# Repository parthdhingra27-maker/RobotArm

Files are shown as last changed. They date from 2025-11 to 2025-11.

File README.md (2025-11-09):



<h1 align="center">UtiliArm: A Custom Open Source 5-DOF Robotic Arm</h1>
<p align="center">Project Files:</p>

<p align="center">
  <a href="https://cad.onshape.com/documents/7d4782fc1d2b81b2411dc364/w/61aa74bc50ffa663fe78e913/e/d61dc358418eba5ccd3d28ce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">Onshape CAD Files</a> •
  <a href="https://docs.google.com/spreadsheets/d/1jZwi7d67DiPdZLEvy5LfeC6HyOPPZ9pO3xaRMX1j6oo/edit?usp=sharing">Bill of Materials</a> •
  <a href="https://blueprint.hackclub.com/projects/599">Blueprint Journal</a>
</p>

I made this to learn more about how robot arms work, how they are designed, controlled, and the types of end-effectors that can be used on them. Once I finish this arm, I want to be able to design different types of end-effectors that can go on the end of this. I also wanted to learn how to design a custom PCB as well as a custom wireless UI that can control this.

## Features
- 5 Degrees of Freedom: The base rotates and tilts, the arm tilts, and the wrist rotates and tilts, allowing for easy movement.
- Cost-Effective: This robot arm with a custom PCB and all parts included costs around $300 to build, making it cost-effective.
- Wireless Control: This arm is powered by an ESP 32 microcontroller with has WIFI capability
- Custom UI: This project also includes a custom UI that will connect to the ESP to control the arm wirelessly from a laptop.
- Encoder Compatibility: This arm uses AS5600 encoders on each stepper motor joint, which allows you to get absolute encoder values and create programs to make the arm go to certain positions.
- Mostly 3D Printed: This arm is mostly 3D printed and doesn't require any machined parts or gearboxes.
- Includes an Emergency Stop
- Will include a fully wireless handheld control panel in the future.

## Design and CAD

The Onshape link can be found at the top of the README.
Each part of the arm is printed separately and then put together using M3 and M4 hardware and heat-set inserts that melt into the plastic using a soldering iron. Bearings are press fit. The pulleys each use a specific belt size, which means there is no need to cut belts. The pulleys are spaced to perfectly fit the belts and tension them properly, which also means no belt tensioners are needed.

This is the base. The top part rotates on bearings and is screwed in from the bottom so it doesn't fall off.



This is the big pulley that tilts the arm. It sits in the bearings, which are shown in the part above.



This is the Arm and the part that holds the arm. It includes a mount on the right side for the AS5600 encoder.




This is the wrist and the part that mounts the wrist onto the arm. The wrist just connects to a stepper motor that allows it to rotate. The wrist uses an MG996R Servo to tilt up and down.




This is the full assembly:



## PCB and Schematics:

This is the schematic for the custom PCB. The arm is powered from a bench power supply. There is a buck converter that converts into 5V. The main microcontroller is an ESP32 and there are three stepper drivers, slots for servo motors, an external Nema 23 driver, an I2C multiplexer for encoders,s and an expansion slot to add another PCB later on. There is also a screw terminal for an E-Stop. The PCB also has a GND pour and VIA's connecting the layers.





## Bill of Materials
These are the components needed. The prices and links can be found here:  <a href="https://docs.google.com/spreadsheets/d/1jZwi7d67DiPdZLEvy5LfeC6HyOPPZ9pO3xaRMX1j6oo/edit?usp=sharing">Bill of Materials Google Sheets</a>

- 1 PCB
- All 3D printed parts
- 3 x Nema 17 Motors
- 1 x Nema 23 Motor
- 3 x TMC2209 Drivers
- 1 x ESP32 Dev Kit
- 1 x TB6600 Driver
- Solder
- Solder Flux
- 3 x AS5600 Magnet Encoders
- 8 x 4x10x4 Bearings
- 8 x 20mm x 47mm x 14mm Bearings
- 1 x GT2 600mm Timing Belt
- 2 x GT2 400mm Timing Belt
- 1 x GT2 420mm Timing Belt
- 5 x 20t Pulleys
- 3 x 5mm to 5mm Shaft Couplers
- 1 x 5mm Shaft
- 8 x 5mm Shaft Collars
- 1 x E-Stop Button
- 1 x TC9548A I2C Multiplexer
- 1 x LM2596 24v to 5v Buck Convertor
- 1 x KF301-2P Screw Terminal
- 1 x XT60 to Banana Plug Cable
- 1 x XT60 to PCB Connector
- 1 x LED
- 1 x 1x3 Headers Pack
- 1 x 1x6 Headers Pack
- 1 x JST-XH-4Pin Connectors Pack
- 1 x 6 Pin Screw Terminals Pack
- 1 x 220R Resistor
- 3 x 0.1uF Capacitors
- 3 x 100 uF Capacitors
- 1 x SS54 Input Diode
- 1 x Pack of M3 M4 Hardware
- 1 x Pack of M4 Heat Set Inserts
- 1 x Pack of Jumper Cables
- 1 x Pack of Heat Shrink for Cables
- 1 x 12x12 Piece of Wood for Base
- 1.5kg x PLA Filament
- 1 x Pack of M2x6mm Philips Head Screws

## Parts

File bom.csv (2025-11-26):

Part Name | Link | Vendor | Qty | Price Per Unit | Total Item Price | Notes | Current Part List (ignore)
Nema 17 Motor | https://www.aliexpress.us/item/3256808273084374.html?mp=1 | Aliexpress | 3 | $5.64 | $16.92 |  | Nema 17 Stepper Motors | TRUE
Nema 23 Motor | https://www.aliexpress.us/item/3256802160042515.html?curPageLogUid=FHrUbtzIm8Mn | Aliexpress | 1 | $23.27 | $23.27 | Cheaper on Amazon | Nema 23 Stepper Motors | TRUE
TMC2209 Drivers | https://www.aliexpress.us/item/2251832841735393.html?curPageLogUid=BcBVglVJW3Tj | Aliexpress | 1 | $13.74 | $13.74 | For Nema 17 Steppers | Stepper Drivers | TRUE
ESP 32 Dev Kit | https://www.amazon.com/ESP-WROOM-32-Development-Microcontroller-Integrated-Compatible/dp/B07WCG1PLV | Amazon | 1 | $8.99 | $8.99 | Cheaper with Shipping on Amazon | Filament - 2kg? | TRUE | Need Gram Amount
TB6600 Driver | https://www.aliexpress.us/item/3256805834107894.html?curPageLogUid=yXXbew8gJGMa | Aliexpress | 1 | $6.24 | $6.24 |  | Small Base Bearings | TRUE
PCB | https://drive.google.com/file/d/11k8NPm6qlL1cPLSDdq3B7cOSP-t6soDT/view?usp=sharing | JLCPCB | 1 | $5.30 | $5.30 | Includes Shipping | GT2 Timing Belt - multiple sizes | TRUE
Solder Flux | https://www.aliexpress.us/item/3256808722589055.html?curPageLogUid=kvXajsBk1s1i | Aliexpress | 1 | $1.95 | $1.95 |  | Big Bearings | TRUE
AS5600 Magnet Sensors | https://www.aliexpress.us/item/3256806163317817.html?curPageLogUid=SWjtwC5qpapB | Aliexpress | 1 | $5.42 | $5.42 | Encoders | Nema Compatible Pulleys | TRUE
Small Base Bearings - 4x10x4 | https://www.aliexpress.us/item/3256808665674212.html?curPageLogUid=9Ovk67vMtHG0 | Aliexpress | 2 | $3.12 | $6.24 |  | Wire - AWG + Jumper Wire | FALSE
6203 Pulley Bearings | https://www.aliexpress.us/item/3256808355977112.html?curPageLogUid=jWwpAysy2Age | Aliexpress | 3 | $4.26 | $12.78 | Cheaper on Amazon than Aliexpress for some reason | Stepper Motor Shaft Coupler | TRUE
Base Timing Belt - GT2 600mm | https://www.aliexpress.us/item/3256804460791382.html?curPageLogUid=6uxZZiebd3DN | Aliexpress | 1 | $3.52 | $3.52 |  | Steppr Motor Shaft Extension | TRUE
Tilt Timing Belt - GT2 400mm | https://www.aliexpress.us/item/3256808692490611.html?curPageLogUid=7w5KFZZBQcLW | Aliexpress | 2 | $4.93 | $9.86 |  | Hall Effect Magnet Sensors | TRUE
Arm Timing Belt - GT2 - 420mm | https://www.aliexpress.us/item/3256804906037786.html?curPageLogUid=88Y1iryqjXZD | Aliexpress | 1 | $3.66 | $3.66 |  | Solder Flux | TRUE
Nema Compatible Pulleys 20t | https://www.amazon.com/WINSINN-Aluminum-Synchronous-Timing-Printer/dp/B077GNZK3J | Amazon | 1 | $6.99 | $6.99 |  | PCB | TRUE
Nema Shaft Coupler - 5mm to 5mm | https://www.aliexpress.us/item/2251832618318567.html?curPageLogUid=BD9rcb5sGai2 | Aliexpress | 3 | $1.30 | $3.90 |  | Incorporate Screen? - already have | TRUE
5mm Shaft | https://www.aliexpress.us/item/3256804855023250.html?curPageLogUid=eToSzEbrcTHk | Aliexpress | 1 | $2.95 | $2.95 |  | Hardware | FALSE
5mm Bore Shaft Collars | https://www.amazon.com/uxcell-Collars-5-05mm-Collar-Carbon/dp/B0D2L23B34 | Amazon | 1 | $7.99 | $7.99 |  | Shaft Coupler | TRUE
Emergency Stop Button | https://www.aliexpress.us/item/3256805247269854.html?curPageLogUid=7iOAle9r2beF | Aliexpress | 1 | $3.16 | $3.16 |  | Shaft Collars | TRUE
TC9548A I2C Multiplexer | https://www.aliexpress.us/item/3256806776881856.html?curPageLogUid=IwMJi6b2YFbL | Aliexpress | 1 | $1.21 | $1.21 |  | Super Glue | TRUE
LM2596 Buck Convertor | https://www.aliexpress.us/item/3256807314089934.html?curPageLogUid=Wu6JDzB64eYc | Aliexpress | 1 | $1.83 | $1.83 |  | Threadlock | TRUE
KF301-2P | https://www.aliexpress.us/item/3256801470316663.html?curPageLogUid=JTMvVZ0UrrPF | Aliexpress | 1 | $2.03 | $2.03 | For 24v Power, TB6600, and EStop | Piece of plywood for base | FALSE
XT60 to Power Supply Cable | https://www.amazon.com/FLY-RC-Connector-Battery-Adapter/dp/B07C1QKNHP | Amazon | 1 | $7.99 | $7.99 |  | Heat Shrink for Wire | FALSE
XT60 to PCB Connector | https://www.aliexpress.us/item/3256807190011486.html?curPageLogUid=VTdH76DwQu0A | Aliexpress | 1 | $1.97 | $1.97 |  | Big Red E-Stop Button | TRUE
LED | https://www.aliexpress.us/item/3256803137393104.html?curPageLogUid=b62xWcd5ozFc | Aliexpress | 1 | $3.93 | $3.93 | For PCB |  | FALSE
1x3 Headers | https://www.aliexpress.us/item/2255800801798474.html?curPageLogUid=KULvQdnglpAk | Aliexpress | 1 | $1.62 | $1.62 | 1x3 Headers for Servo |  | FALSE
1x6 Headers | https://www.aliexpress.us/item/2255800801798474.html?curPageLogUid=KULvQdnglpAk | Aliexpress | 1 | $1.62 | $1.62 | 1x6 Header for the Expansion Slot on PCB | Electronics | FALSE
JST-XH-4Pin Connectors | https://www.aliexpress.us/item/3256806894018733.html?curPageLogUid=TLIAWzMVtzoH | Aliexpress | 1 | $2.41 | $2.41 | Stepper Connectors for the PCB |  | FALSE
6 Pin Screw Terminal | https://www.aliexpress.us/item/3256802765387985.html?curPageLogUid=IgnuE5tFisnK | Aliexpress | 1 | $2.98 | $2.98 | For TB6600 Data Connector | Esp 32 | TRUE
220R Resistor for LED | https://www.aliexpress.us/item/2251832766343175.html?curPageLogUid=BYePsJeal4NR | Aliexpress | 1 | $1.32 | $1.32 |  | Buck convertor | TRUE
0.1uF Capacitor for Drivers | https://www.digikey.com/en/products/detail/kemet/C0805C104K5RACTU/411169 | DigiKey | 3 | $0.08 | $0.24 | 4.99 shipping for DigiKey. Included in total | JST-XH 4-pin extension cables | FALSE
100uF Capacitor for Drivers | https://www.digikey.com/en/products/detail/rubycon/35ZLH100MEFC6-3X11/3134256 | DigiKey | 3 | $0.32 | $0.96 |  |  | FALSE
SS54 Input Diode | https://www.digikey.com/en/products/detail/shenzhen-slkormicro-semicon-co-ltd/SS54/21853075 | DigiKey | 1 | $0.18 | $0.18 |  |  | FALSE
M3 M4 Hardware | https://www.aliexpress.us/item/2255799852960451.html?mp=1 | Aliexpress | 1 | $14.00 | $14.00 | All the fasteners needed for the arm |  | FALSE
Heat Sunk Inserts | https://www.amazon.com/Inserts-3D-Printing-Accessories-Compatible-Soldering-Threaded/dp/B0CDRZN4B2 | Amazon | 1 | $8.99 | $8.99 | For all the hardware to plastic connections |  | FALSE
Jumper Cables | https://www.amazon.com/California-JOS-Breadboard-Optional-Multicolored/dp/B0BRTJXND9 | Amazon | 1 | $5.97 | $5.97 |  |  | FALSE
18 AWG Wire | https://www.aliexpress.us/item/3256806379805687.html?mp=1 | Aliexpress | 1 | $2.41 | $2.41 | Needed to connect the E-Stop |  | FALSE
Heat Shrink Wrap | https://www.aliexpress.us/item/3256807959988149.html?mp=1 | Aliexpress | 1 | $2.79 | $2.79 |  |  | FALSE
12x12 Piece of Wood | https://www.lowes.com/pd/Unbranded-1-4-in-x-2-ft-x-2-ft-Pine-Sanded-Plywood/5001992857 | Lowes | 1 | $7.78 | $7.78 | Piece of wood for the base of the robot to screw into and to mount electronics to. Cheapest one I could find |  | FALSE
M2x6mm Philips Screws | https://www.aliexpress.us/item/3256802119350443.html?curPageLogUid=bYjfPRmE1l1c | Aliexpress | 1 | $1.40 | $1.40 | For mounting the AS5600 Encoders |  | FALSE
 |  |  |  |  |  |  |  | FALSE
 |  |  |  |  |  |  |  | FALSE
 |  |  |  |  |  |  |  | FALSE
 |  |  |  |  |  |  |  | FALSE
Parts Total | $216.51 |  |  |  |  |  |  | FALSE
Shipping Total | $4.99 |  |  |  |  |  |  | FALSE
Subtotal | $221.50 |  |  |  |  |  |  | FALSE
Tax (Virginia 4.5%) | $9.97 |  |  |  |  |  |  | FALSE
Project Total | $231.47 |  |  |  |  |  |  | FALSE
 |  |  |  |  |  |  |  | FALSE
 |  |  |  |  |  |  |  | FALSE
 |  |  |  |  |  |  |  | FALSE
 |  |  |  |  |  |  |  | FALSE
 |  |  |  |  |  |  |  | FALSE
 |  |  |  |  |  |  |  | FALSE
 |  |  |  |  |  |  |  | FALSE
 |  |  |  |  |  |  |  | FALSE
 |  |  |  |  |  |  |  | FALSE
 |  |  |  |  |  |  |  | FALSE
 |  |  |  |  |  |  |  | FALSE
 |  |  |  |  |  |  |  | FALSE
 |  |  |  |  |  |  |  | FALSE
 |  |  |  |  |  |  |  | FALSE
 |  |  |  |  |  |  |  | FALSE
 |  |  |  |  |  |  |  | FALSE
 |  |  |  |  |  |  |  | FALSE
 |  |  |  |  |  |  |  | FALSE
 |  |  |  |  |  |  |  | FALSE
 |  |  |  |  |  |  |  | FALSE
 |  |  |  |  |  |  |  | FALSE
 |  |  |  |  |  |  |  | FALSE
 |  |  |  |  |  |  |  | FALSE
 |  |  |  |  |  |  |  | FALSE
 |  |  |  |  |  |  |  | FALSE
 |  |  |  |  |  |  |  | FALSE
 |  |  |  |  |  |  |  | FALSE
 |  |  |  |  |  |  |  | FALSE
 |  |  |  |  |  |  |  | FALSE
 |  |  |  |  |  |  |  | FALSE
 |  |  |  |  |  |  |  | FALSE
 |  |  |  |  |  |  |  | FALSE
 |  |  |  |  |  |  |  | FALSE
 |  |  |  |  |  |  |  | FALSE
 |  |  |  |  |  |  |  | FALSE
 |  |  |  |  |  |  |  | FALSE
 |  |  |  |  |  |  |  | FALSE
 |  |  |  |  |  |  |  | FALSE
 |  |  |  |  |  |  |  | FALSE
 |  |  |  |  |  |  |  | FALSE
 |  |  |  |  |  |  |  | FALSE
 |  |  |  |  |  |  |  | FALSE
 |  |  |  |  |  |  |  | FALSE
 |  |  |  |  |  |  |  | FALSE
 |  |  |  |  |  |  |  | FALSE
 |  |  |  |  |  |  |  | FALSE
 |  |  |  |  |  |  |  | FALSE
 |  |  |  |  |  |  |  | FALSE
 |  |  |  |  |  |  |  | FALSE
 |  |  |  |  |  |  |  | FALSE
 |  |  |  |  |  |  |  | FALSE
 |  |  |  |  |  |  |  | FALSE
 |  |  |  |  |  |  |  | FALSE
 |  |  |  |  |  |  |  | FALSE
 |  |  |  |  |  |  |  | FALSE
 |  |  |  |  |  |  |  | FALSE
 |  |  |  |  |  |  |  | FALSE
 |  |  |  |  |  |  |  | FALSE
 |  |  |  |  |  |  |  | FALSE
 |  |  |  |  |  |  |  | FALSE
 |  |  |  |  |  |  |  | FALSE
 |  |  |  |  |  |  |  | FALSE
 |  |  |  |  |  |  |  | FALSE
 |  |  |  |  |  |  |  | FALSE
 |  |  |  |  |  |  |  | FALSE
 |  |  |  |  |  |  |  | FALSE
 |  |  |  |  |  |  |  | FALSE
 |  |  |  |  |  |  |  | FALSE
 |  |  |  |  |  |  |  | FALSE
 |  |  |  |  |  |  |  | FALSE
 |  |  |  |  |  |  |  | FALSE
 |  |  |  |  |  |  |  | FALSE
 |  |  |  |  |  |  |  | FALSE
 |  |  |  |  |  |  |  | FALSE
 |  |  |  |  |  |  |  | FALSE
 |  |  |  |  |  |  |  | FALSE
 |  |  |  |  |  |  |  | FALSE
 |  |  |  |  |  |  |  | FALSE
 |  |  |  |  |  |  |  | FALSE
 |  |  |  |  |  |  |  | FALSE
 |  |  |  |  |  |  |  | FALSE
 |  |  |  |  |  |  |  | FALSE
 |  |  |  |  |  |  |  | FALSE
 |  |  |  |  |  |  |  | FALSE
 |  |  |  |  |  |  |  | FALSE
 |  |  |  |  |  |  |  | FALSE
 |  |  |  |  |  |  |  | FALSE
 |  |  |  |  |  |  |  | FALSE
 |  |  |  |  |  |  |  | FALSE
 |  |  |  |  |  |  |  | FALSE
 |  |  |  |  |  |  |  | FALSE
 |  |  |  |  |  |  |  | FALSE
 |  |  |  |  |  |  |  | FALSE
 |  |  |  |  |  |  |  | FALSE
 |  |  |  |  |  |  |  | FALSE
 |  |  |  |  |  |  |  | FALSE
 |  |  |  |  |  |  |  | FALSE
 |  |  |  |  |  |  |  | FALSE
 |  |  |  |  |  |  |  | FALSE
 |  |  |  |  |  |  |  | FALSE
 |  |  |  |  |  |  |  | FALSE
 |  |  |  |  |  |  |  | FALSE
 |  |  |  |  |  |  |  | FALSE
 |  |  |  |  |  |  |  | FALSE
 |  |  |  |  |  |  |  | FALSE
 |  |  |  |  |  |  |  | FALSE
 |  |  |  |  |  |  |  | FALSE
 |  |  |  |  |  |  |  | FALSE
 |  |  |  |  |  |  |  | FALSE
 |  |  |  |  |  |  |  | FALSE
 |  |  |  |  |  |  |  | FALSE
 |  |  |  |  |  |  |  | FALSE
 |  |  |  |  |  |  |  | FALSE
 |  |  |  |  |  |  |  | FALSE
 |  |  |  |  |  |  |  | FALSE
 |  |  |  |  |  |  |  | FALSE
 |  |  |  |  |  |  |  | FALSE
 |  |  |  |  |  |  |  | FALSE
 |  |  |  |  |  |  |  | FALSE
 |  |  |  |  |  |  |  | FALSE
 |  |  |  |  |  |  |  | FALSE
 |  |  |  |  |  |  |  | FALSE
 |  |  |  |  |  |  |  | FALSE
 |  |  |  |  |  |  |  | FALSE
 |  |  |  |  |  |  |  | FALSE
 |  |  |  |  |  |  |  | FALSE
 |  |  |  |  |  |  |  | FALSE
 |  |  |  |  |  |  |  | FALSE
 |  |  |  |  |  |  |  | FALSE
 |  |  |  |  |  |  |  | FALSE
 |  |  |  |  |  |  |  | FALSE
 |  |  |  |  |  |  |  | FALSE
 |  |  |  |  |  |  |  | FALSE
 |  |  |  |  |  |  |  | FALSE
 |  |  |  |  |  |  |  | FALSE
 |  |  |  |  |  |  |  | FALSE
 |  |  |  |  |  |  |  | FALSE
 |  |  |  |  |  |  |  | FALSE
 |  |  |  |  |  |  |  | FALSE
 |  |  |  |  |  |  |  | FALSE
 |  |  |  |  |  |  |  | FALSE
 |  |  |  |  |  |  |  | FALSE
 |  |  |  |  |  |  |  | FALSE
 |  |  |  |  |  |  |  | FALSE
 |  |  |  |  |  |  |  | FALSE
 |  |  |  |  |  |  |  | FALSE
 |  |  |  |  |  |  |  | FALSE
 |  |  |  |  |  |  |  | FALSE
 |  |  |  |  |  |  |  | FALSE
 |  |  |  |  |  |  |  | FALSE
 |  |  |  |  |  |  |  | FALSE
 |  |  |  |  |  |  |  | FALSE
 |  |  |  |  |  |  |  | FALSE
 |  |  |  |  |  |  |  | FALSE
 |  |  |  |  |  |  |  | FALSE
 |  |  |  |  |  |  |  | FALSE
 |  |  |  |  |  |  |  | FALSE
 |  |  |  |  |  |  |  | FALSE
 |  |  |  |  |  |  |  | FALSE
 |  |  |  |  |  |  |  | FALSE
 |  |  |  |  |  |  |  | FALSE
 |  |  |  |  |  |  |  | FALSE
 |  |  |  |  |  |  |  | FALSE
 |  |  |  |  |  |  |  | FALSE
 |  |  |  |  |  |  |  | FALSE
 |  |  |  |  |  |  |  | FALSE
 |  |  |  |  |  |  |  | FALSE
 |  |  |  |  |  |  |  | FALSE
 |  |  |  |  |  |  |  | FALSE
 |  |  |  |  |  |  |  | FALSE
 |  |  |  |  |  |  |  | FALSE
 |  |  |  |  |  |  |  | FALSE
 |  |  |  |  |  |  |  | FALSE
 |  |  |  |  |  |  |  | FALSE
 |  |  |  |  |  |  |  | FALSE
 |  |  |  |  |  |  |  | FALSE
 |  |  |  |  |  |  |  | FALSE
 |  |  |  |  |  |  |  | FALSE
 |  |  |  |  |  |  |  | FALSE
 |  |  |  |  |  |  |  | FALSE
 |  |  |  |  |  |  |  | FALSE
 |  |  |  |  |  |  |  | FALSE
 |  |  |  |  |  |  |  | FALSE
 |  |  |  |  |  |  |  | FALSE
 |  |  |  |  |  |  |  | FALSE
 |  |  |  |  |  |  |  | FALSE
 |  |  |  |  |  |  |  | FALSE
 |  |  |  |  |  |  |  | FALSE
 |  |  |  |  |  |  |  | FALSE
 |  |  |  |  |  |  |  | FALSE
 |  |  |  |  |  |  |  | FALSE
 |  |  |  |  |  |  |  | FALSE
 |  |  |  |  |  |  |  | FALSE
 |  |  |  |  |  |  |  | FALSE
 |  |  |  |  |  |  |  | FALSE
 |  |  |  |  |  |  |  | FALSE
 |  |  |  |  |  |  |  | FALSE
 |  |  |  |  |  |  |  | FALSE
 |  |  |  |  |  |  |  | FALSE
 |  |  |  |  |  |  |  | FALSE
 |  |  |  |  |  |  |  | FALSE
 |  |  |  |  |  |  |  | FALSE
 |  |  |  |  |  |  |  | FALSE
 |  |  |  |  |  |  |  | FALSE
 |  |  |  |  |  |  |  | FALSE
 |  |  |  |  |  |  |  | FALSE
 |  |  |  |  |  |  |  | FALSE
 |  |  |  |  |  |  |  | FALSE
 |  |  |  |  |  |  |  | FALSE
 |  |  |  |  |  |  |  | FALSE
 |  |  |  |  |  |  |  | FALSE
 |  |  |  |  |  |  |  | FALSE
 |  |  |  |  |  |  |  | FALSE
 |  |  |  |  |  |  |  | FALSE
 |  |  |  |  |  |  |  | FALSE
 |  |  |  |  |  |  |  | FALSE
 |  |  |  |  |  |  |  | FALSE
 |  |  |  |  |  |  |  | FALSE
 |  |  |  |  |  |  |  | FALSE
 |  |  |  |  |  |  |  | FALSE
 |  |  |  |  |  |  |  | FALSE
 |  |  |  |  |  |  |  | FALSE
 |  |  |  |  |  |  |  | FALSE
 |  |  |  |  |  |  |  | FALSE
 |  |  |  |  |  |  |  | FALSE
 |  |  |  |  |  |  |  | FALSE
 |  |  |  |  |  |  |  | FALSE
 |  |  |  |  |  |  |  | FALSE
 |  |  |  |  |  |  |  | FALSE
 |  |  |  |  |  |  |  | FALSE
 |  |  |  |  |  |  |  | FALSE
 |  |  |  |  |  |  |  | FALSE
 |  |  |  |  |  |  |  | FALSE
 |  |  |  |  |  |  |  | FALSE
 |  |  |  |  |  |  |  | FALSE
 |  |  |  |  |  |  |  | FALSE
 |  |  |  |  |  |  |  | FALSE
 |  |  |  |  |  |  |  | FALSE
 |  |  |  |  |  |  |  | FALSE
 |  |  |  |  |  |  |  | FALSE
 |  |  |  |  |  |  |  | FALSE
 |  |  |  |  |  |  |  | FALSE
 |  |  |  |  |  |  |  | FALSE
 |  |  |  |  |  |  |  | FALSE
 |  |  |  |  |  |  |  | FALSE
 |  |  |  |  |  |  |  | FALSE
 |  |  |  |  |  |  |  | FALSE
 |  |  |  |  |  |  |  | FALSE
 |  |  |  |  |  |  |  | FALSE
 |  |  |  |  |  |  |  | FALSE
 |  |  |  |  |  |  |  | FALSE
 |  |  |  |  |  |  |  | FALSE
 |  |  |  |  |  |  |  | FALSE
 |  |  |  |  |  |  |  | FALSE
 |  |  |  |  |  |  |  | FALSE
 |  |  |  |  |  |  |  | FALSE
 |  |  |  |  |  |  |  | FALSE
 |  |  |  |  |  |  |  | FALSE
 |  |  |  |  |  |  |  | FALSE
 |  |  |  |  |  |  |  | FALSE
 |  |  |  |  |  |  |  | FALSE
 |  |  |  |  |  |  |  | FALSE
 |  |  |  |  |  |  |  | FALSE
 |  |  |  |  |  |  |  | FALSE
 |  |  |  |  |  |  |  | FALSE
 |  |  |  |  |  |  |  | FALSE
 |  |  |  |  |  |  |  | FALSE
 |  |  |  |  |  |  |  | FALSE
 |  |  |  |  |  |  |  | FALSE
 |  |  |  |  |  |  |  | FALSE
 |  |  |  |  |  |  |  | FALSE
 |  |  |  |  |  |  |  | FALSE
 |  |  |  |  |  |  |  | FALSE
 |  |  |  |  |  |  |  | FALSE
 |  |  |  |  |  |  |  | FALSE
 |  |  |  |  |  |  |  | FALSE
 |  |  |  |  |  |  |  | FALSE
 |  |  |  |  |  |  |  | FALSE
 |  |  |  |  |  |  |  | FALSE
 |  |  |  |  |  |  |  | FALSE
 |  |  |  |  |  |  |  | FALSE
 |  |  |  |  |  |  |  | FALSE
 |  |  |  |  |  |  |  | FALSE
 |  |  |  |  |  |  |  | FALSE
 |  |  |  |  |  |  |  | FALSE
 |  |  |  |  |  |  |  | FALSE
 |  |  |  |  |  |  |  | FALSE
 |  |  |  |  |  |  |  | FALSE
 |  |  |  |  |  |  |  | FALSE
 |  |  |  |  |  |  |  | FALSE
 |  |  |  |  |  |  |  | FALSE
 |  |  |  |  |  |  |  | FALSE
 |  |  |  |  |  |  |  | FALSE
 |  |  |  |  |  |  |  | FALSE
 |  |  |  |  |  |  |  | FALSE
 |  |  |  |  |  |  |  | FALSE
 |  |  |  |  |  |  |  | FALSE
 |  |  |  |  |  |  |  | FALSE
 |  |  |  |  |  |  |  | FALSE
 |  |  |  |  |  |  |  | FALSE
 |  |  |  |  |  |  |  | FALSE
 |  |  |  |  |  |  |  | FALSE
 |  |  |  |  |  |  |  | FALSE
 |  |  |  |  |  |  |  | FALSE
 |  |  |  |  |  |  |  | FALSE
 |  |  |  |  |  |  |  | FALSE
 |  |  |  |  |  |  |  | FALSE
 |  |  |  |  |  |  |  | FALSE
 |  |  |  |  |  |  |  | FALSE
 |  |  |  |  |  |  |  | FALSE
 |  |  |  |  |  |  |  | FALSE
 |  |  |  |  |  |  |  | FALSE
 |  |  |  |  |  |  |  | FALSE
 |  |  |  |  |  |  |  | FALSE
 |  |  |  |  |  |  |  | FALSE
 |  |  |  |  |  |  |  | FALSE
 |  |  |  |  |  |  |  | FALSE
 |  |  |  |  |  |  |  | FALSE
 |  |  |  |  |  |  |  | FALSE
 |  |  |  |  |  |  |  | FALSE
 |  |  |  |  |  |  |  | FALSE
 |  |  |  |  |  |  |  | FALSE
 |  |  |  |  |  |  |  | FALSE
 |  |  |  |  |  |  |  | FALSE
 |  |  |  |  |  |  |  | FALSE
 |  |  |  |  |  |  |  | FALSE
 |  |  |  |  |  |  |  | FALSE
 |  |  |  |  |  |  |  | FALSE
 |  |  |  |  |  |  |  | FALSE
 |  |  |  |  |  |  |  | FALSE
 |  |  |  |  |  |  |  | FALSE
 |  |  |  |  |  |  |  | FALSE
 |  |  |  |  |  |  |  | FALSE
 |  |  |  |  |  |  |  | FALSE
 |  |  |  |  |  |  |  | FALSE
 |  |  |  |  |  |  |  | FALSE
 |  |  |  |  |  |  |  | FALSE
 |  |  |  |  |  |  |  | FALSE
 |  |  |  |  |  |  |  | FALSE
 |  |  |  |  |  |  |  | FALSE
 |  |  |  |  |  |  |  | FALSE
 |  |  |  |  |  |  |  | FALSE
 |  |  |  |  |  |  |  | FALSE
 |  |  |  |  |  |  |  | FALSE
 |  |  |  |  |  |  |  | FALSE
 |  |  |  |  |  |  |  | FALSE
 |  |  |  |  |  |  |  | FALSE
 |  |  |  |  |  |  |  | FALSE
 |  |  |  |  |  |  |  | FALSE
 |  |  |  |  |  |  |  | FALSE
 |  |  |  |  |  |  |  | FALSE
 |  |  |  |  |  |  |  | FALSE
 |  |  |  |  |  |  |  | FALSE
 |  |  |  |  |  |  |  | FALSE
 |  |  |  |  |  |  |  | FALSE
 |  |  |  |  |  |  |  | FALSE
 |  |  |  |  |  |  |  | FALSE
 |  |  |  |  |  |  |  | FALSE
 |  |  |  |  |  |  |  | FALSE
 |  |  |  |  |  |  |  | FALSE
 |  |  |  |  |  |  |  | FALSE
 |  |  |  |  |  |  |  | FALSE
 |  |  |  |  |  |  |  | FALSE
 |  |  |  |  |  |  |  | FALSE
 |  |  |  |  |  |  |  | FALSE
 |  |  |  |  |  |  |  | FALSE
 |  |  |  |  |  |  |  | FALSE
 |  |  |  |  |  |  |  | FALSE
 |  |  |  |  |  |  |  | FALSE
 |  |  |  |  |  |  |  | FALSE
 |  |  |  |  |  |  |  | FALSE
 |  |  |  |  |  |  |  | FALSE
 |  |  |  |  |  |  |  | FALSE
 |  |  |  |  |  |  |  | FALSE
 |  |  |  |  |  |  |  | FALSE
 |  |  |  |  |  |  |  | FALSE
 |  |  |  |  |  |  |  | FALSE
 |  |  |  |  |  |  |  | FALSE
 |  |  |  |  |  |  |  | FALSE
 |  |  |  |  |  |  |  | FALSE
 |  |  |  |  |  |  |  | FALSE
 |  |  |  |  |  |  |  | FALSE
 |  |  |  |  |  |  |  | FALSE
 |  |  |  |  |  |  |  | FALSE
 |  |  |  |  |  |  |  | FALSE
 |  |  |  |  |  |  |  | FALSE
 |  |  |  |  |  |  |  | FALSE
 |  |  |  |  |  |  |  | FALSE
 |  |  |  |  |  |  |  | FALSE
 |  |  |  |  |  |  |  | FALSE
 |  |  |  |  |  |  |  | FALSE
 |  |  |  |  |  |  |  | FALSE
 |  |  |  |  |  |  |  | FALSE
 |  |  |  |  |  |  |  | FALSE
 |  |  |  |  |  |  |  | FALSE
 |  |  |  |  |  |  |  | FALSE
 |  |  |  |  |  |  |  | FALSE
 |  |  |  |  |  |  |  | FALSE
 |  |  |  |  |  |  |  | FALSE
 |  |  |  |  |  |  |  | FALSE
 |  |  |  |  |  |  |  | FALSE
 |  |  |  |  |  |  |  | FALSE
 |  |  |  |  |  |  |  | FALSE
 |  |  |  |  |  |  |  | FALSE
 |  |  |  |  |  |  |  | FALSE
 |  |  |  |  |  |  |  | FALSE
 |  |  |  |  |  |  |  | FALSE
 |  |  |  |  |  |  |  | FALSE
 |  |  |  |  |  |  |  | FALSE
 |  |  |  |  |  |  |  | FALSE
 |  |  |  |  |  |  |  | FALSE
 |  |  |  |  |  |  |  | FALSE
 |  |  |  |  |  |  |  | FALSE
 |  |  |  |  |  |  |  | FALSE
 |  |  |  |  |  |  |  | FALSE
 |  |  |  |  |  |  |  | FALSE
 |  |  |  |  |  |  |  | FALSE
 |  |  |  |  |  |  |  | FALSE
 |  |  |  |  |  |  |  | FALSE
 |  |  |  |  |  |  |  | FALSE
 |  |  |  |  |  |  |  | FALSE
 |  |  |  |  |  |  |  | FALSE
 |  |  |  |  |  |  |  | FALSE
 |  |  |  |  |  |  |  | FALSE
 |  |  |  |  |  |  |  | FALSE
 |  |  |  |  |  |  |  | FALSE
 |  |  |  |  |  |  |  | FALSE
 |  |  |  |  |  |  |  | FALSE
 |  |  |  |  |  |  |  | FALSE
 |  |  |  |  |  |  |  | FALSE
 |  |  |  |  |  |  |  | FALSE
 |  |  |  |  |  |  |  | FALSE
 |  |  |  |  |  |  |  | FALSE
 |  |  |  |  |  |  |  | FALSE
 |  |  |  |  |  |  |  | FALSE
 |  |  |  |  |  |  |  | FALSE
 |  |  |  |  |  |  |  | FALSE
 |  |  |  |  |  |  |  | FALSE
 |  |  |  |  |  |  |  | FALSE
 |  |  |  |  |  |  |  | FALSE
 |  |  |  |  |  |  |  | FALSE
 |  |  |  |  |  |  |  | FALSE
 |  |  |  |  |  |  |  | FALSE
 |  |  |  |  |  |  |  | FALSE
 |  |  |  |  |  |  |  | FALSE
 |  |  |  |  |  |  |  | FALSE
 |  |  |  |  |  |  |  | FALSE
 |  |  |  |  |  |  |  | FALSE
 |  |  |  |  |  |  |  | FALSE
 |  |  |  |  |  |  |  | FALSE
 |  |  |  |  |  |  |  | FALSE
 |  |  |  |  |  |  |  | FALSE
 |  |  |  |  |  |  |  | FALSE
 |  |  |  |  |  |  |  | FALSE
 |  |  |  |  |  |  |  | FALSE
 |  |  |  |  |  |  |  | FALSE
 |  |  |  |  |  |  |  | FALSE
 |  |  |  |  |  |  |  | FALSE
 |  |  |  |  |  |  |  | FALSE
 |  |  |  |  |  |  |  | FALSE
 |  |  |  |  |  |  |  | FALSE
 |  |  |  |  |  |  |  | FALSE
 |  |  |  |  |  |  |  | FALSE
 |  |  |  |  |  |  |  | FALSE
 |  |  |  |  |  |  |  | FALSE
 |  |  |  |  |  |  |  | FALSE
 |  |  |  |  |  |  |  | FALSE
 |  |  |  |  |  |  |  | FALSE
 |  |  |  |  |  |  |  | FALSE
 |  |  |  |  |  |  |  | FALSE
 |  |  |  |  |  |  |  | FALSE
 |  |  |  |  |  |  |  | FALSE
 |  |  |  |  |  |  |  | FALSE
 |  |  |  |  |  |  |  | FALSE
 |  |  |  |  |  |  |  | FALSE
 |  |  |  |  |  |  |  | FALSE
 |  |  |  |  |  |  |  | FALSE
 |  |  |  |  |  |  |  | FALSE
 |  |  |  |  |  |  |  | FALSE
 |  |  |  |  |  |  |  | FALSE
 |  |  |  |  |  |  |  | FALSE
 |  |  |  |  |  |  |  | FALSE
 |  |  |  |  |  |  |  | FALSE
 |  |  |  |  |  |  |  | FALSE
 |  |  |  |  |  |  |  | FALSE
 |  |  |  |  |  |  |  | FALSE
 |  |  |  |  |  |  |  | FALSE
 |  |  |  |  |  |  |  | FALSE
 |  |  |  |  |  |  |  | FALSE
 |  |  |  |  |  |  |  | FALSE
 |  |  |  |  |  |  |  | FALSE
 |  |  |  |  |  |  |  | FALSE
 |  |  |  |  |  |  |  | FALSE
 |  |  |  |  |  |  |  | FALSE
 |  |  |  |  |  |  |  | FALSE
 |  |  |  |  |  |  |  | FALSE
 |  |  |  |  |  |  |  | FALSE
 |  |  |  |  |  |  |  | FALSE
 |  |  |  |  |  |  |  | FALSE
 |  |  |  |  |  |  |  | FALSE
 |  |  |  |  |  |  |  | FALSE
 |  |  |  |  |  |  |  | FALSE
 |  |  |  |  |  |  |  | FALSE
 |  |  |  |  |  |  |  | FALSE
 |  |  |  |  |  |  |  | FALSE
 |  |  |  |  |  |  |  | FALSE
 |  |  |  |  |  |  |  | FALSE
 |  |  |  |  |  |  |  | FALSE
 |  |  |  |  |  |  |  | FALSE
 |  |  |  |  |  |  |  | FALSE
 |  |  |  |  |  |  |  | FALSE
 |  |  |  |  |  |  |  | FALSE
 |  |  |  |  |  |  |  | FALSE
 |  |  |  |  |  |  |  | FALSE
 |  |  |  |  |  |  |  | FALSE
 |  |  |  |  |  |  |  | FALSE
 |  |  |  |  |  |  |  | FALSE
 |  |  |  |  |  |  |  | FALSE
 |  |  |  |  |  |  |  | FALSE
 |  |  |  |  |  |  |  | FALSE
 |  |  |  |  |  |  |  | FALSE
 |  |  |  |  |  |  |  | FALSE
 |  |  |  |  |  |  |  | FALSE
 |  |  |  |  |  |  |  | FALSE
 |  |  |  |  |  |  |  | FALSE
 |  |  |  |  |  |  |  | FALSE
 |  |  |  |  |  |  |  | FALSE
 |  |  |  |  |  |  |  | FALSE
 |  |  |  |  |  |  |  | FALSE
 |  |  |  |  |  |  |  | FALSE
 |  |  |  |  |  |  |  | FALSE
 |  |  |  |  |  |  |  | FALSE
 |  |  |  |  |  |  |  | FALSE
 |  |  |  |  |  |  |  | FALSE
 |  |  |  |  |  |  |  | FALSE
 |  |  |  |  |  |  |  | FALSE
 |  |  |  |  |  |  |  | FALSE
 |  |  |  |  |  |  |  | FALSE
 |  |  |  |  |  |  |  | FALSE
 |  |  |  |  |  |  |  | FALSE
 |  |  |  |  |  |  |  | FALSE
 |  |  |  |  |  |  |  | FALSE
 |  |  |  |  |  |  |  | FALSE
 |  |  |  |  |  |  |  | FALSE
 |  |  |  |  |  |  |  | FALSE
 |  |  |  |  |  |  |  | FALSE
 |  |  |  |  |  |  |  | FALSE
 |  |  |  |  |  |  |  | FALSE
 |  |  |  |  |  |  |  | FALSE
 |  |  |  |  |  |  |  | FALSE
 |  |  |  |  |  |  |  | FALSE
 |  |  |  |  |  |  |  | FALSE
 |  |  |  |  |  |  |  | FALSE
 |  |  |  |  |  |  |  | FALSE
 |  |  |  |  |  |  |  | FALSE
 |  |  |  |  |  |  |  | FALSE
 |  |  |  |  |  |  |  | FALSE
 |  |  |  |  |  |  |  | FALSE
 |  |  |  |  |  |  |  | FALSE
 |  |  |  |  |  |  |  | FALSE
 |  |  |  |  |  |  |  | FALSE
 |  |  |  |  |  |  |  | FALSE
 |  |  |  |  |  |  |  | FALSE
 |  |  |  |  |  |  |  | FALSE
 |  |  |  |  |  |  |  | FALSE
 |  |  |  |  |  |  |  | FALSE
 |  |  |  |  |  |  |  | FALSE
 |  |  |  |  |  |  |  | FALSE
 |  |  |  |  |  |  |  | FALSE
 |  |  |  |  |  |  |  | FALSE
 |  |  |  |  |  |  |  | FALSE
 |  |  |  |  |  |  |  | FALSE
 |  |  |  |  |  |  |  | FALSE
 |  |  |  |  |  |  |  | FALSE
 |  |  |  |  |  |  |  | FALSE
 |  |  |  |  |  |  |  | FALSE
 |  |  |  |  |  |  |  | FALSE
 |  |  |  |  |  |  |  | FALSE
 |  |  |  |  |  |  |  | FALSE
 |  |  |  |  |  |  |  | FALSE
 |  |  |  |  |  |  |  | FALSE
 |  |  |  |  |  |  |  | FALSE
 |  |  |  |  |  |  |  | FALSE
 |  |  |  |  |  |  |  | FALSE
 |  |  |  |  |  |  |  | FALSE
 |  |  |  |  |  |  |  | FALSE
 |  |  |  |  |  |  |  | FALSE
 |  |  |  |  |  |  |  | FALSE
 |  |  |  |  |  |  |  | FALSE
 |  |  |  |  |  |  |  | FALSE
 |  |  |  |  |  |  |  | FALSE
 |  |  |  |  |  |  |  | FALSE
 |  |  |  |  |  |  |  | FALSE
 |  |  |  |  |  |  |  | FALSE
 |  |  |  |  |  |  |  | FALSE
 |  |  |  |  |  |  |  | FALSE
 |  |  |  |  |  |  |  | FALSE
 |  |  |  |  |  |  |  | FALSE
 |  |  |  |  |  |  |  | FALSE
 |  |  |  |  |  |  |  | FALSE
 |  |  |  |  |  |  |  | FALSE
 |  |  |  |  |  |  |  | FALSE
 |  |  |  |  |  |  |  | FALSE
 |  |  |  |  |  |  |  | FALSE
 |  |  |  |  |  |  |  | FALSE
 |  |  |  |  |  |  |  | FALSE
 |  |  |  |  |  |  |  | FALSE
 |  |  |  |  |  |  |  | FALSE
 |  |  |  |  |  |  |  | FALSE
 |  |  |  |  |  |  |  | FALSE
 |  |  |  |  |  |  |  | FALSE
 |  |  |  |  |  |  |  | FALSE
 |  |  |  |  |  |  |  | FALSE
 |  |  |  |  |  |  |  | FALSE
 |  |  |  |  |  |  |  | FALSE
 |  |  |  |  |  |  |  | FALSE
 |  |  |  |  |  |  |  | FALSE
 |  |  |  |  |  |  |  | FALSE
 |  |  |  |  |  |  |  | FALSE
 |  |  |  |  |  |  |  | FALSE
 |  |  |  |  |  |  |  | FALSE
 |  |  |  |  |  |  |  | FALSE
 |  |  |  |  |  |  |  | FALSE
 |  |  |  |  |  |  |  | FALSE
 |  |  |  |  |  |  |  | FALSE
 |  |  |  |  |  |  |  | FALSE
 |  |  |  |  |  |  |  | FALSE
 |  |  |  |  |  |  |  | FALSE
 |  |  |  |  |  |  |  | FALSE
 |  |  |  |  |  |  |  | FALSE
 |  |  |  |  |  |  |  | FALSE
 |  |  |  |  |  |  |  | FALSE
 |  |  |  |  |  |  |  | FALSE
 |  |  |  |  |  |  |  | FALSE
 |  |  |  |  |  |  |  | FALSE
 |  |  |  |  |  |  |  | FALSE
 |  |  |  |  |  |  |  | FALSE
 |  |  |  |  |  |  |  | FALSE
 |  |  |  |  |  |  |  | FALSE
 |  |  |  |  |  |  |  | FALSE
 |  |  |  |  |  |  |  | FALSE
 |  |  |  |  |  |  |  | FALSE
 |  |  |  |  |  |  |  | FALSE
 |  |  |  |  |  |  |  | FALSE
 |  |  |  |  |  |  |  | FALSE
 |  |  |  |  |  |  |  | FALSE
 |  |  |  |  |  |  |  | FALSE
 |  |  |  |  |  |  |  | FALSE
 |  |  |  |  |  |  |  | FALSE
 |  |  |  |  |  |  |  | FALSE
 |  |  |  |  |  |  |  | FALSE
 |  |  |  |  |  |  |  | FALSE
 |  |  |  |  |  |  |  | FALSE
 |  |  |  |  |  |  |  | FALSE
 |  |  |  |  |  |  |  | FALSE
 |  |  |  |  |  |  |  | FALSE
 |  |  |  |  |  |  |  | FALSE
 |  |  |  |  |  |  |  | FALSE
 |  |  |  |  |  |  |  | FALSE
 |  |  |  |  |  |  |  | FALSE
 |  |  |  |  |  |  |  | FALSE
 |  |  |  |  |  |  |  | FALSE
 |  |  |  |  |  |  |  | FALSE
 |  |  |  |  |  |  |  | FALSE
 |  |  |  |  |  |  |  | FALSE
 |  |  |  |  |  |  |  | FALSE
 |  |  |  |  |  |  |  | FALSE
 |  |  |  |  |  |  |  | FALSE
 |  |  |  |  |  |  |  | FALSE
 |  |  |  |  |  |  |  | FALSE
 |  |  |  |  |  |  |  | FALSE
 |  |  |  |  |  |  |  | FALSE
 |  |  |  |  |  |  |  | FALSE
 |  |  |  |  |  |  |  | FALSE
 |  |  |  |  |  |  |  | FALSE
 |  |  |  |  |  |  |  | FALSE
 |  |  |  |  |  |  |  | FALSE
 |  |  |  |  |  |  |  | FALSE
 |  |  |  |  |  |  |  | FALSE
 |  |  |  |  |  |  |  | FALSE
 |  |  |  |  |  |  |  | FALSE
 |  |  |  |  |  |  |  | FALSE
 |  |  |  |  |  |  |  | FALSE
 |  |  |  |  |  |  |  | FALSE
 |  |  |  |  |  |  |  | FALSE
 |  |  |  |  |  |  |  | FALSE
 |  |  |  |  |  |  |  | FALSE
 |  |  |  |  |  |  |  | FALSE
 |  |  |  |  |  |  |  | FALSE
 |  |  |  |  |  |  |  | FALSE
 |  |  |  |  |  |  |  | FALSE
 |  |  |  |  |  |  |  | FALSE
 |  |  |  |  |  |  |  | FALSE
 |  |  |  |  |  |  |  | FALSE
 |  |  |  |  |  |  |  | FALSE
 |  |  |  |  |  |  |  | FALSE
 |  |  |  |  |  |  |  | FALSE
 |  |  |  |  |  |  |  | FALSE
 |  |  |  |  |  |  |  | FALSE
 |  |  |  |  |  |  |  | FALSE
 |  |  |  |  |  |  |  | FALSE
 |  |  |  |  |  |  |  | FALSE
 |  |  |  |  |  |  |  | FALSE
 |  |  |  |  |  |  |  | FALSE
 |  |  |  |  |  |  |  | FALSE
 |  |  |  |  |  |  |  | FALSE
 |  |  |  |  |  |  |  | FALSE
 |  |  |  |  |  |  |  | FALSE
 |  |  |  |  |  |  |  | FALSE
 |  |  |  |  |  |  |  | FALSE
 |  |  |  |  |  |  |  | FALSE
 |  |  |  |  |  |  |  | FALSE
 |  |  |  |  |  |  |  | FALSE
 |  |  |  |  |  |  |  | FALSE
 |  |  |  |  |  |  |  | FALSE
 |  |  |  |  |  |  |  | FALSE
 |  |  |  |  |  |  |  | FALSE
 |  |  |  |  |  |  |  | FALSE
 |  |  |  |  |  |  |  | FALSE
 |  |  |  |  |  |  |  | FALSE
 |  |  |  |  |  |  |  | FALSE
 |  |  |  |  |  |  |  | FALSE
 |  |  |  |  |  |  |  | FALSE
 |  |  |  |  |  |  |  | FALSE
 |  |  |  |  |  |  |  | FALSE
 |  |  |  |  |  |  |  | FALSE
 |  |  |  |  |  |  |  | FALSE
 |  |  |  |  |  |  |  | FALSE
 |  |  |  |  |  |  |  | FALSE
 |  |  |  |  |  |  |  | FALSE
 |  |  |  |  |  |  |  | FALSE
 |  |  |  |  |  |  |  | FALSE
 |  |  |  |  |  |  |  | FALSE
 |  |  |  |  |  |  |  | FALSE
 |  |  |  |  |  |  |  | FALSE
 |  |  |  |  |  |  |  | FALSE
 |  |  |  |  |  |  |  | FALSE
 |  |  |  |  |  |  |  | FALSE
 |  |  |  |  |  |  |  | FALSE
 |  |  |  |  |  |  |  | FALSE
 |  |  |  |  |  |  |  | FALSE
 |  |  |  |  |  |  |  | FALSE
 |  |  |  |  |  |  |  | FALSE
 |  |  |  |  |  |  |  | FALSE
 |  |  |  |  |  |  |  | FALSE
 |  |  |  |  |  |  |  | FALSE
 |  |  |  |  |  |  |  | FALSE
 |  |  |  |  |  |  |  | FALSE
 |  |  |  |  |  |  |  | FALSE
 |  |  |  |  |  |  |  | FALSE
 |  |  |  |  |  |  |  | FALSE
 |  |  |  |  |  |  |  | FALSE
 |  |  |  |  |  |  |  | FALSE
 |  |  |  |  |  |  |  | FALSE
 |  |  |  |  |  |  |  | FALSE
 |  |  |  |  |  |  |  | FALSE
 |  |  |  |  |  |  |  | FALSE
 |  |  |  |  |  |  |  | FALSE
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

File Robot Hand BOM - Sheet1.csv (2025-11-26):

Part Name | Link | Vendor | Qty | Price Per Unit | Total Item Price | Notes
Fishing Line (300M-CODE1.5-25LB) | https://www.aliexpress.us/item/3256806677560595.html?curPageLogUid=xqlwFctEmkCP | Aliexpress | 1 | $3.68 | $3.68
Elastic Band (2mm 10meters) | https://www.aliexpress.us/item/3256803466347856.html?curPageLogUid=SwbsAVxUO2GD | Aliexpress | 1 | $1.75 | $1.75
MG996R Servo Motors | https://www.aliexpress.us/item/3256807958407137.html?curPageLogUid=x0eCaFTvWNqL | Aliexpress | 5 | $3.54 | $17.70
Glove for Gesture Control | https://www.aliexpress.us/item/3256806453163489.html?curPageLogUid=y11qQYStVuEl | Aliexpress | 2 | $1.54 | $3.08 | Quantity two, one for human hand, one for robot hand to make it look professional
PCB | Screenshot | JCLPCB | 1 | $9.28 | $9.28 | Price with shipping
Flex Sensors | https://www.adafruit.com/product/1070 | Adafruit | 5 | $7.95 | $39.75 | $5 shipping for Adafruit
Force Sensors FSR402 | https://www.aliexpress.us/item/3256801705862124.html?curPageLogUid=u7hCV1u7F19a | Aliexpress | 5 | $2.11 | $10.55 | For fingertips
ESP32 | https://www.amazon.com/ESP-WROOM-32-Development-Dual-Mode-Microcontroller-Integrated/dp/B07WCG1PLV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 | Amazon | 1 | $8.99 | $8.99
M4 Bolt 45mm | https://www.aliexpress.us/item/3256805692722422.html?curPageLogUid=1TE9tD01TeyL | Aliexpress | 1 | $1.77 | $1.77 | For thumb joint
M4 Bolt 65mm | https://www.aliexpress.us/item/3256805692722422.html?curPageLogUid=1TE9tD01TeyL | Aliexpress | 1 | $2.31 | $2.31 | For ring and pinky finger joint
M3 Heat Set Inserts (4.2 OD 4mmL) | https://www.aliexpress.us/item/3256803396040989.html?curPageLogUid=uiCawpZkTW66 | Aliexpress | 1 | $2.03 | $2.03 | For Servo Motors Mounting
6x2 Magnets | https://www.aliexpress.us/item/3256809140919864.html?curPageLogUid=9g5VtP7lFqCs | Aliexpress | 1 | $3.03 | $3.03 | For mounting the top of the forearm
XH-M404 Buck Convertor | https://www.aliexpress.us/item/3256806242694144.html?curPageLogUid=DJq7uOqj9dBd | Aliexpress | 1 | $2.49 | $2.49 | Output to 6v for Servo's
JSTXH Connector and Wire | https://www.aliexpress.us/item/3256807274583113.html?curPageLogUid=7WYmVla5wsYM | Aliexpress | 2 | $1.64 | $3.28 | For sensor connectors
10k Resistors | https://www.adafruit.com/product/2784 | Adafruit | 1 | $0.75 | $0.75 | For force sensors
47k Resistors | https://www.adafruit.com/product/2786 | Adafruit | 1 | $0.75 | $0.75 | For flex sensors
ADS1115 ADC Input Board | https://www.aliexpress.us/item/3256807442377637.html?curPageLogUid=CpsMpuDdoTgi | Aliexpress | 1 | $2.40 | $2.40 | For connecting force sensors
M3 Hardware | https://www.aliexpress.us/item/3256806973435795.html?curPageLogUid=rohvX8p8T95O | Aliexpress | 1 | $8.88 | $8.88
JSTXH-2P | https://www.aliexpress.us/item/3256806894018733.html | Aliexpress | 1 | $1.60 | $1.60
3 Pin Headers | https://www.aliexpress.us/item/2255800801798474.html | Aliexpress | 1 | $1.46 | $1.46
JSTXH-4P | https://www.aliexpress.us/item/3256806894018733.html | Aliexpress | 1 | $2.33 | $2.33
2 Wire Screw Terminals | https://www.aliexpress.us/item/3256801470316663.html | Aliexpress | 1 | $1.91 | $1.91
1.5mm Metal Rod (20mm length) | https://www.aliexpress.us/item/2255800287548941.html?curPageLogUid=AwWHSz7JHJuQ | Aliexpress | 1 | $1.99 | $1.99 | To connect each joint together
Parts Total | $131.76
Shipping Total | $5.00 | Adafruit Shipping
Subtotal | $136.76
Tax (Virginia 4.5%) | $6.15
Project Total | $142.91

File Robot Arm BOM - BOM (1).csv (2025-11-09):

Part Name | Link | Vendor | Qty | Price Per Unit | Total Item Price | Notes | Current Part List (ignore)
Nema 17 Motor | https://www.amazon.com/STEPPERONLINE-Stepper-Bipolar-Connector-compatible/dp/B00PNEQKC0 | Amazon | 3 | $13.99 | $41.97 | Cheaper on Amazon | Nema 17 Stepper Motors | TRUE
Nema 23 Motor | https://www.amazon.com/STEPPERONLINE-Stepper-178-5oz-1-26Nm-Stepping/dp/B00PNEPF5I | Amazon | 1 | $25.99 | $25.99 | Cheaper on Amazon | Nema 23 Stepper Motors | TRUE
TMC2209 Drivers | https://www.amazon.com/BIGTREETECH-TMC2209-Stepper-Stepstick-Motherboard/dp/B07ZPYKL46 | Amazon | 1 | $22.99 | $22.99 | For Nema 17 Steppers | Stepper Drivers | TRUE
ESP 32 Dev Kit | https://www.amazon.com/ESP-WROOM-32-Development-Microcontroller-Integrated-Compatible/dp/B07WCG1PLV | Amazon | 1 | $8.99 | $8.99 | Cheaper with Shipping on Amazon | Filament - 2kg? | TRUE | Need Gram Amount
TB6600 Driver | https://www.amazon.com/Stepper-DC9-42V-Subdivision-Controller-MicroStepping/dp/B08SG7L54W | Amazon | 1 | $10.89 | $10.89 | Same price as Aliexpress | Small Base Bearings | TRUE
PCB | https://drive.google.com/file/d/1B4Z1Hi-BUxl28VFVw4MLdO5dm2JzmmHV/view?usp=sharing | PCBWAY | 1 | $12.80 | $12.80 | 5 PCB with Shipping | GT2 Timing Belt - multiple sizes | TRUE
Solder Flux | https://www.aliexpress.us/item/3256808722589055.html?curPageLogUid=kvXajsBk1s1i | Aliexpress | 1 | $1.95 | $1.95 |  | Big Bearings | TRUE
AS5600 Magnet Sensors | https://www.aliexpress.us/item/3256806163317817.html?curPageLogUid=SWjtwC5qpapB | Aliexpress | 1 | $5.42 | $5.42 | Encoders | Nema Compatible Pulleys | TRUE
 |  |  |  |  |  |  | Bench Power Supply | TRUE
Small Base Bearings - 4x10x4 | https://www.aliexpress.us/item/3256808665674212.html?curPageLogUid=9Ovk67vMtHG0 | Aliexpress | 2 | $3.12 | $6.24 |  | Wire - AWG + Jumper Wire | FALSE
Pulley Bearings | https://www.amazon.com/gp/product/B07X1YPDQR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 | Amazon | 1 | $19.99 | $19.99 | Cheaper on Amazon | Stepper Motor Shaft Coupler | TRUE
Base Timing Belt - GT2 600mm | https://www.aliexpress.us/item/3256804460791382.html?curPageLogUid=6uxZZiebd3DN | Aliexpress | 1 | $3.52 | $3.52 |  | Steppr Motor Shaft Extension | TRUE
Tilt Timing Belt - GT2 400mm | https://www.aliexpress.us/item/3256808692490611.html?curPageLogUid=7w5KFZZBQcLW | Aliexpress | 2 | $4.93 | $9.86 |  | Hall Effect Magnet Sensors | TRUE
Arm Timing Belt - GT2 - 420mm | https://www.aliexpress.us/item/3256804906037786.html?curPageLogUid=88Y1iryqjXZD | Aliexpress | 1 | $3.66 | $3.66 |  | Solder Flux | TRUE
Nema Compatible Pulleys 20t | https://www.amazon.com/WINSINN-Aluminum-Synchronous-Timing-Printer/dp/B077GNZK3J | Amazon | 1 | $6.99 | $6.99 |  | PCB | TRUE
Nema Shaft Coupler - 5mm to 5mm | https://www.amazon.com/ZYCST-Aluminium-Coupling-Connector-Airplane/dp/B07QQM472Q | Amazon | 1 | $8.68 | $8.68 |  | Incorporate Screen? - already have | TRUE
5mm Shaft | https://www.aliexpress.us/item/3256804855023250.html?curPageLogUid=eToSzEbrcTHk | Aliexpress | 1 | $2.95 | $2.95 |  | Hardware | FALSE
 |  |  |  |  |  |  | Heat Sunk Inserts | FALSE
5mm Bore Shaft Collars | https://www.amazon.com/uxcell-Collars-5-05mm-Collar-Carbon/dp/B0D2L23B34 | Amazon | 1 | $7.99 | $7.99 |  | Shaft Coupler | TRUE
Emergency Stop Button | https://www.aliexpress.us/item/3256805247269854.html?curPageLogUid=7iOAle9r2beF | Aliexpress | 1 | $3.16 | $3.16 |  | Shaft Collars | TRUE
TC9548A I2C Multiplexer | https://www.aliexpress.us/item/3256806776881856.html?curPageLogUid=IwMJi6b2YFbL | Aliexpress | 1 | $1.21 | $1.21 |  | Super Glue | TRUE
LM2596 Buck Convertor | https://www.aliexpress.us/item/3256807314089934.html?curPageLogUid=Wu6JDzB64eYc | Aliexpress | 1 | $1.83 | $1.83 |  | Threadlock | TRUE
KF301-2P | https://www.aliexpress.us/item/3256801470316663.html?curPageLogUid=JTMvVZ0UrrPF | Aliexpress | 1 | $2.03 | $2.03 | For 24v Power, TB6600, and EStop | Piece of plywood for base | FALSE
XT60 to Power Supply Cable | https://www.amazon.com/FLY-RC-Connector-Battery-Adapter/dp/B07C1QKNHP | Amazon | 1 | $7.99 | $7.99 |  | Heat Shrink for Wire | FALSE
XT60 to PCB Connector | https://www.aliexpress.us/item/3256807190011486.html?curPageLogUid=VTdH76DwQu0A | Aliexpress | 1 | $1.97 | $1.97 |  | Big Red E-Stop Button | TRUE
LED | https://www.aliexpress.us/item/3256803137393104.html?curPageLogUid=b62xWcd5ozFc | Aliexpress | 1 | $3.93 | $3.93 | For PCB |  | FALSE
1x3 Headers | https://www.aliexpress.us/item/2255800801798474.html?curPageLogUid=KULvQdnglpAk | Aliexpress | 1 | $1.62 | $1.62 | 1x3 Headers for Servo |  | FALSE
1x6 Headers | https://www.aliexpress.us/item/2255800801798474.html?curPageLogUid=KULvQdnglpAk | Aliexpress | 1 | $1.62 | $1.62 | 1x6 Header for the Expansion Slot on PCB | Electronics | FALSE
JST-XH-4Pin Connectors | https://www.aliexpress.us/item/3256806894018733.html?curPageLogUid=TLIAWzMVtzoH | Aliexpress | 1 | $2.41 | $2.41 | Stepper Connectors for the PCB |  | FALSE
6 Pin Screw Terminal | https://www.aliexpress.us/item/3256802765387985.html?curPageLogUid=IgnuE5tFisnK | Aliexpress | 1 | $2.98 | $2.98 | For TB6600 Data Connector | Esp 32 | TRUE
220R Resistor for LED | https://www.aliexpress.us/item/2251832766343175.html?curPageLogUid=BYePsJeal4NR | Aliexpress | 1 | $1.32 | $1.32 |  | Buck convertor | TRUE
0.1uF Capacitor for Drivers | https://www.digikey.com/en/products/detail/kemet/C0805C104K5RACTU/411169 | DigiKey | 3 | $0.08 | $0.24 | 4.99 shipping for DigiKey. Included in total | JST-XH 4-pin extension cables | FALSE
100uF Capacitor for Drivers | https://www.digikey.com/en/products/detail/rubycon/35ZLH100MEFC6-3X11/3134256 | DigiKey | 3 | $0.32 | $0.96 |  |  | FALSE
SS54 Input Diode | https://www.digikey.com/en/products/detail/shenzhen-slkormicro-semicon-co-ltd/SS54/21853075 | DigiKey | 1 | $0.18 | $0.18 |  |  | FALSE
Hardware | https://www.amazon.com/Kadrick-Assortment-M2-M3-M4/dp/B0CQJZCC9T | Amazon | 1 | $21.99 | $21.99 | All the fasteners needed for the arm |  | FALSE
Heat Sunk Inserts | https://www.amazon.com/Inserts-3D-Printing-Accessories-Compatible-Soldering-Threaded/dp/B0CDRZN4B2 | Amazon | 1 | $8.99 | $8.99 | For all the hardware to plastic connections |  | FALSE
Jumper Cables | https://www.amazon.com/California-JOS-Breadboard-Optional-Multicolored/dp/B0BRTJXND9 | Amazon | 1 | $5.97 | $5.97 |  |  | FALSE
18 AWG Wire | https://www.aliexpress.us/item/3256806379805687.html?mp=1 | Aliexpress | 1 | $2.41 | $2.41 | Needed to connect the E-Stop |  | FALSE
Heat Shrink Wrap | https://www.aliexpress.us/item/3256807959988149.html?mp=1 | Aliexpress | 1 | $2.79 | $2.79 |  |  | FALSE
12x12 Piece of Wood | https://www.amazon.com/Plywood-Stronger-Basswood-Cutting-Woodpeckers/dp/B0CLWCM6J2 | Amazon | 1 | $6.44 | $6.44 | Piece of wood for the base of the robot to screw into and to mount electronics to. Cheapest one I could find |  | FALSE
Elegoo PLA Filament - Black | https://www.amazon.com/ELEGOO-Filament-Printing-Dimensional-Cardboard/dp/B0C6XG88RG | Amazon | 0.5 | $15.99 | $8.00 | I need 1500g of filament so I will buy half this kg myself which is why it says 0.5 qty |  | FALSE
Elegoo PLA Filament - Blue | https://www.amazon.com/ELEGOO-Filament-Printing-Dimensional-Cardboard/dp/B0CD2JK7TJ | Amazon | 1 | $18.99 | $18.99 |  |  | FALSE
M2x6mm Philips Screws | https://www.aliexpress.us/item/3256802119350443.html?curPageLogUid=bYjfPRmE1l1c | Aliexpress | 1 | $1.40 | $1.40 | For mounting the AS5600 Encoders |  | FALSE
 |  |  |  |  |  |  |  | FALSE
 |  |  |  |  |  |  |  | FALSE
Parts Total | $311.31 |  |  |  |  |  |  | FALSE
Shipping Total | $4.99 |  |  |  |  |  |  | FALSE
Subtotal | $316.30 |  |  |  |  |  |  | FALSE
Tax (Virginia 6%) | $18.98 |  |  |  |  |  |  | FALSE
Project Total | $335.27 |  |  |  |  |  |  | FALSE
 |  |  |  |  |  |  |  | FALSE
 |  |  |  |  |  |  |  | FALSE
 |  |  |  |  |  |  |  | FALSE
 |  |  |  |  |  |  |  | FALSE
 |  |  |  |  |  |  |  | FALSE
 |  |  |  |  |  |  |  | FALSE
 |  |  |  |  |  |  |  | FALSE
 |  |  |  |  |  |  |  | FALSE
 |  |  |  |  |  |  |  | FALSE
 |  |  |  |  |  |  |  | FALSE
 |  |  |  |  |  |  |  | FALSE
 |  |  |  |  |  |  |  | FALSE
 |  |  |  |  |  |  |  | FALSE
 |  |  |  |  |  |  |  | FALSE
 |  |  |  |  |  |  |  | FALSE
 |  |  |  |  |  |  |  | FALSE
 |  |  |  |  |  |  |  | FALSE
 |  |  |  |  |  |  |  | FALSE
 |  |  |  |  |  |  |  | FALSE
 |  |  |  |  |  |  |  | FALSE
 |  |  |  |  |  |  |  | FALSE
 |  |  |  |  |  |  |  | FALSE
 |  |  |  |  |  |  |  | FALSE
 |  |  |  |  |  |  |  | FALSE
 |  |  |  |  |  |  |  | FALSE
 |  |  |  |  |  |  |  | FALSE
 |  |  |  |  |  |  |  | FALSE
 |  |  |  |  |  |  |  | FALSE
 |  |  |  |  |  |  |  | FALSE
 |  |  |  |  |  |  |  | FALSE
 |  |  |  |  |  |  |  | FALSE
 |  |  |  |  |  |  |  | FALSE
 |  |  |  |  |  |  |  | FALSE
 |  |  |  |  |  |  |  | FALSE
 |  |  |  |  |  |  |  | FALSE
 |  |  |  |  |  |  |  | FALSE
 |  |  |  |  |  |  |  | FALSE
 |  |  |  |  |  |  |  | FALSE
 |  |  |  |  |  |  |  | FALSE
 |  |  |  |  |  |  |  | FALSE
 |  |  |  |  |  |  |  | FALSE
 |  |  |  |  |  |  |  | FALSE
 |  |  |  |  |  |  |  | FALSE
 |  |  |  |  |  |  |  | FALSE
 |  |  |  |  |  |  |  | FALSE
 |  |  |  |  |  |  |  | FALSE
 |  |  |  |  |  |  |  | FALSE
 |  |  |  |  |  |  |  | FALSE
 |  |  |  |  |  |  |  | FALSE
 |  |  |  |  |  |  |  | FALSE
 |  |  |  |  |  |  |  | FALSE
 |  |  |  |  |  |  |  | FALSE
 |  |  |  |  |  |  |  | FALSE
 |  |  |  |  |  |  |  | FALSE
 |  |  |  |  |  |  |  | FALSE
 |  |  |  |  |  |  |  | FALSE
 |  |  |  |  |  |  |  | FALSE
 |  |  |  |  |  |  |  | FALSE
 |  |  |  |  |  |  |  | FALSE
 |  |  |  |  |  |  |  | FALSE
 |  |  |  |  |  |  |  | FALSE
 |  |  |  |  |  |  |  | FALSE
 |  |  |  |  |  |  |  | FALSE
 |  |  |  |  |  |  |  | FALSE
 |  |  |  |  |  |  |  | FALSE
 |  |  |  |  |  |  |  | FALSE
 |  |  |  |  |  |  |  | FALSE
 |  |  |  |  |  |  |  | FALSE
 |  |  |  |  |  |  |  | FALSE
 |  |  |  |  |  |  |  | FALSE
 |  |  |  |  |  |  |  | FALSE
 |  |  |  |  |  |  |  | FALSE
 |  |  |  |  |  |  |  | FALSE
 |  |  |  |  |  |  |  | FALSE
 |  |  |  |  |  |  |  | FALSE
 |  |  |  |  |  |  |  | FALSE
 |  |  |  |  |  |  |  | FALSE
 |  |  |  |  |  |  |  | FALSE
 |  |  |  |  |  |  |  | FALSE
 |  |  |  |  |  |  |  | FALSE
 |  |  |  |  |  |  |  | FALSE
 |  |  |  |  |  |  |  | FALSE
 |  |  |  |  |  |  |  | FALSE
 |  |  |  |  |  |  |  | FALSE
 |  |  |  |  |  |  |  | FALSE
 |  |  |  |  |  |  |  | FALSE
 |  |  |  |  |  |  |  | FALSE
 |  |  |  |  |  |  |  | FALSE
 |  |  |  |  |  |  |  | FALSE
 |  |  |  |  |  |  |  | FALSE
 |  |  |  |  |  |  |  | FALSE
 |  |  |  |  |  |  |  | FALSE
 |  |  |  |  |  |  |  | FALSE
 |  |  |  |  |  |  |  | FALSE
 |  |  |  |  |  |  |  | FALSE
 |  |  |  |  |  |  |  | FALSE
 |  |  |  |  |  |  |  | FALSE
 |  |  |  |  |  |  |  | FALSE
 |  |  |  |  |  |  |  | FALSE
 |  |  |  |  |  |  |  | FALSE
 |  |  |  |  |  |  |  | FALSE
 |  |  |  |  |  |  |  | FALSE
 |  |  |  |  |  |  |  | FALSE
 |  |  |  |  |  |  |  | FALSE
 |  |  |  |  |  |  |  | FALSE
 |  |  |  |  |  |  |  | FALSE
 |  |  |  |  |  |  |  | FALSE
 |  |  |  |  |  |  |  | FALSE
 |  |  |  |  |  |  |  | FALSE
 |  |  |  |  |  |  |  | FALSE
 |  |  |  |  |  |  |  | FALSE
 |  |  |  |  |  |  |  | FALSE
 |  |  |  |  |  |  |  | FALSE
 |  |  |  |  |  |  |  | FALSE
 |  |  |  |  |  |  |  | FALSE
 |  |  |  |  |  |  |  | FALSE
 |  |  |  |  |  |  |  | FALSE
 |  |  |  |  |  |  |  | FALSE
 |  |  |  |  |  |  |  | FALSE
 |  |  |  |  |  |  |  | FALSE
 |  |  |  |  |  |  |  | FALSE
 |  |  |  |  |  |  |  | FALSE
 |  |  |  |  |  |  |  | FALSE
 |  |  |  |  |  |  |  | FALSE
 |  |  |  |  |  |  |  | FALSE
 |  |  |  |  |  |  |  | FALSE
 |  |  |  |  |  |  |  | FALSE
 |  |  |  |  |  |  |  | FALSE
 |  |  |  |  |  |  |  | FALSE
 |  |  |  |  |  |  |  | FALSE
 |  |  |  |  |  |  |  | FALSE
 |  |  |  |  |  |  |  | FALSE
 |  |  |  |  |  |  |  | FALSE
 |  |  |  |  |  |  |  | FALSE
 |  |  |  |  |  |  |  | FALSE
 |  |  |  |  |  |  |  | FALSE
 |  |  |  |  |  |  |  | FALSE
 |  |  |  |  |  |  |  | FALSE
 |  |  |  |  |  |  |  | FALSE
 |  |  |  |  |  |  |  | FALSE
 |  |  |  |  |  |  |  | FALSE
 |  |  |  |  |  |  |  | FALSE
 |  |  |  |  |  |  |  | FALSE
 |  |  |  |  |  |  |  | FALSE
 |  |  |  |  |  |  |  | FALSE
 |  |  |  |  |  |  |  | FALSE
 |  |  |  |  |  |  |  | FALSE
 |  |  |  |  |  |  |  | FALSE
 |  |  |  |  |  |  |  | FALSE
 |  |  |  |  |  |  |  | FALSE
 |  |  |  |  |  |  |  | FALSE
 |  |  |  |  |  |  |  | FALSE
 |  |  |  |  |  |  |  | FALSE
 |  |  |  |  |  |  |  | FALSE
 |  |  |  |  |  |  |  | FALSE
 |  |  |  |  |  |  |  | FALSE
 |  |  |  |  |  |  |  | FALSE
 |  |  |  |  |  |  |  | FALSE
 |  |  |  |  |  |  |  | FALSE
 |  |  |  |  |  |  |  | FALSE
 |  |  |  |  |  |  |  | FALSE
 |  |  |  |  |  |  |  | FALSE
 |  |  |  |  |  |  |  | FALSE
 |  |  |  |  |  |  |  | FALSE
 |  |  |  |  |  |  |  | FALSE
 |  |  |  |  |  |  |  | FALSE
 |  |  |  |  |  |  |  | FALSE
 |  |  |  |  |  |  |  | FALSE
 |  |  |  |  |  |  |  | FALSE
 |  |  |  |  |  |  |  | FALSE
 |  |  |  |  |  |  |  | FALSE
 |  |  |  |  |  |  |  | FALSE
 |  |  |  |  |  |  |  | FALSE
 |  |  |  |  |  |  |  | FALSE
 |  |  |  |  |  |  |  | FALSE
 |  |  |  |  |  |  |  | FALSE
 |  |  |  |  |  |  |  | FALSE
 |  |  |  |  |  |  |  | FALSE
 |  |  |  |  |  |  |  | FALSE
 |  |  |  |  |  |  |  | FALSE
 |  |  |  |  |  |  |  | FALSE
 |  |  |  |  |  |  |  | FALSE
 |  |  |  |  |  |  |  | FALSE
 |  |  |  |  |  |  |  | FALSE
 |  |  |  |  |  |  |  | FALSE
 |  |  |  |  |  |  |  | FALSE
 |  |  |  |  |  |  |  | FALSE
 |  |  |  |  |  |  |  | FALSE
 |  |  |  |  |  |  |  | FALSE
 |  |  |  |  |  |  |  | FALSE
 |  |  |  |  |  |  |  | FALSE
 |  |  |  |  |  |  |  | FALSE
 |  |  |  |  |  |  |  | FALSE
 |  |  |  |  |  |  |  | FALSE
 |  |  |  |  |  |  |  | FALSE
 |  |  |  |  |  |  |  | FALSE
 |  |  |  |  |  |  |  | FALSE
 |  |  |  |  |  |  |  | FALSE
 |  |  |  |  |  |  |  | FALSE
 |  |  |  |  |  |  |  | FALSE
 |  |  |  |  |  |  |  | FALSE
 |  |  |  |  |  |  |  | FALSE
 |  |  |  |  |  |  |  | FALSE
 |  |  |  |  |  |  |  | FALSE
 |  |  |  |  |  |  |  | FALSE
 |  |  |  |  |  |  |  | FALSE
 |  |  |  |  |  |  |  | FALSE
 |  |  |  |  |  |  |  | FALSE
 |  |  |  |  |  |  |  | FALSE
 |  |  |  |  |  |  |  | FALSE
 |  |  |  |  |  |  |  | FALSE
 |  |  |  |  |  |  |  | FALSE
 |  |  |  |  |  |  |  | FALSE
 |  |  |  |  |  |  |  | FALSE
 |  |  |  |  |  |  |  | FALSE
 |  |  |  |  |  |  |  | FALSE
 |  |  |  |  |  |  |  | FALSE
 |  |  |  |  |  |  |  | FALSE
 |  |  |  |  |  |  |  | FALSE
 |  |  |  |  |  |  |  | FALSE
 |  |  |  |  |  |  |  | FALSE
 |  |  |  |  |  |  |  | FALSE
 |  |  |  |  |  |  |  | FALSE
 |  |  |  |  |  |  |  | FALSE
 |  |  |  |  |  |  |  | FALSE
 |  |  |  |  |  |  |  | FALSE
 |  |  |  |  |  |  |  | FALSE
 |  |  |  |  |  |  |  | FALSE
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

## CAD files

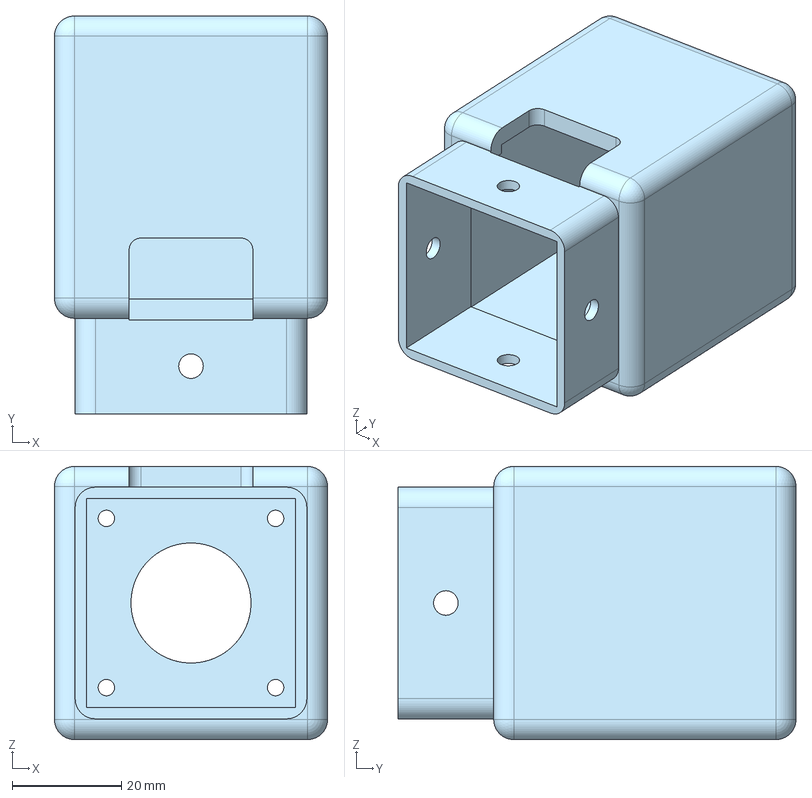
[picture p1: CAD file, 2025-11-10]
CAD/WRIST Part Studio - Wrist Stepper Mount.step
50.0 x 72.9 x 50.0 mm

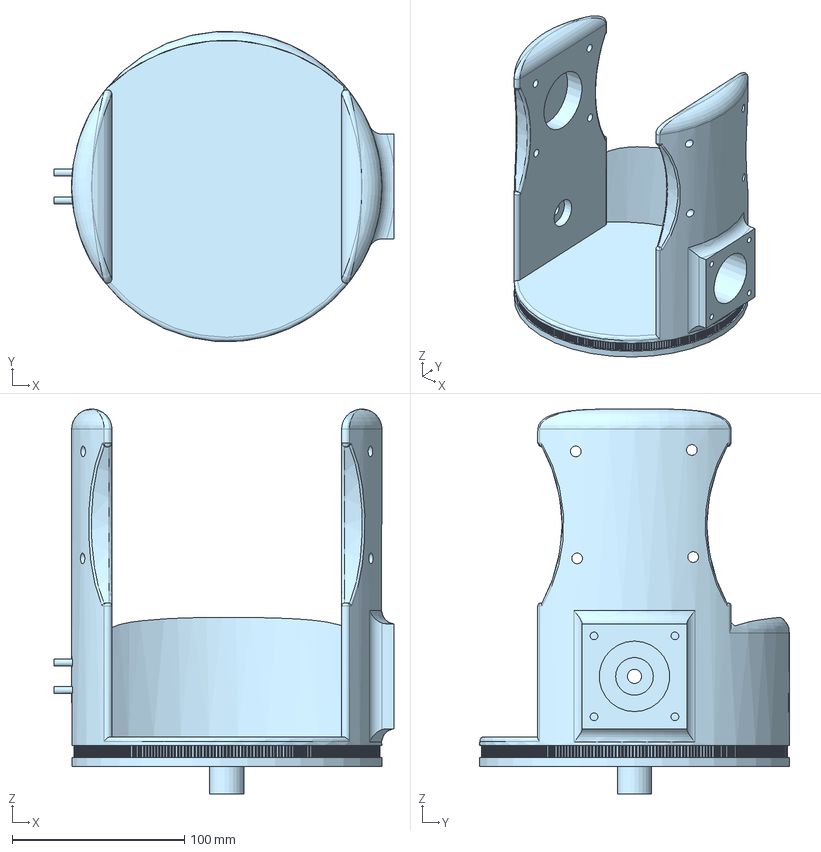
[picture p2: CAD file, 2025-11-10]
CAD/BASE Part Studio - PART B - Rotation (1).step
197.4 x 180.2 x 223.7 mm

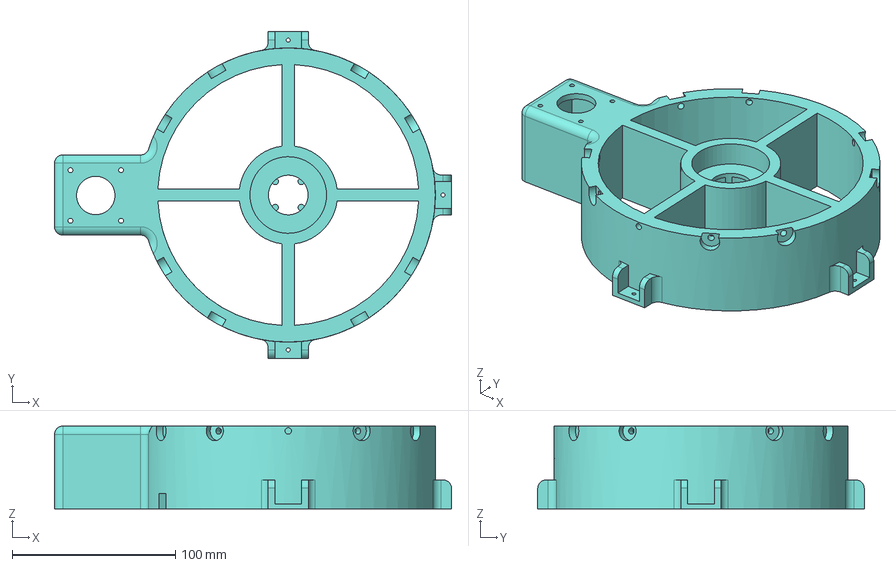
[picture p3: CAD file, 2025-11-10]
CAD/BASE Part Studio - PART A - Base (1).step
243.4 x 200.2 x 50.8 mm

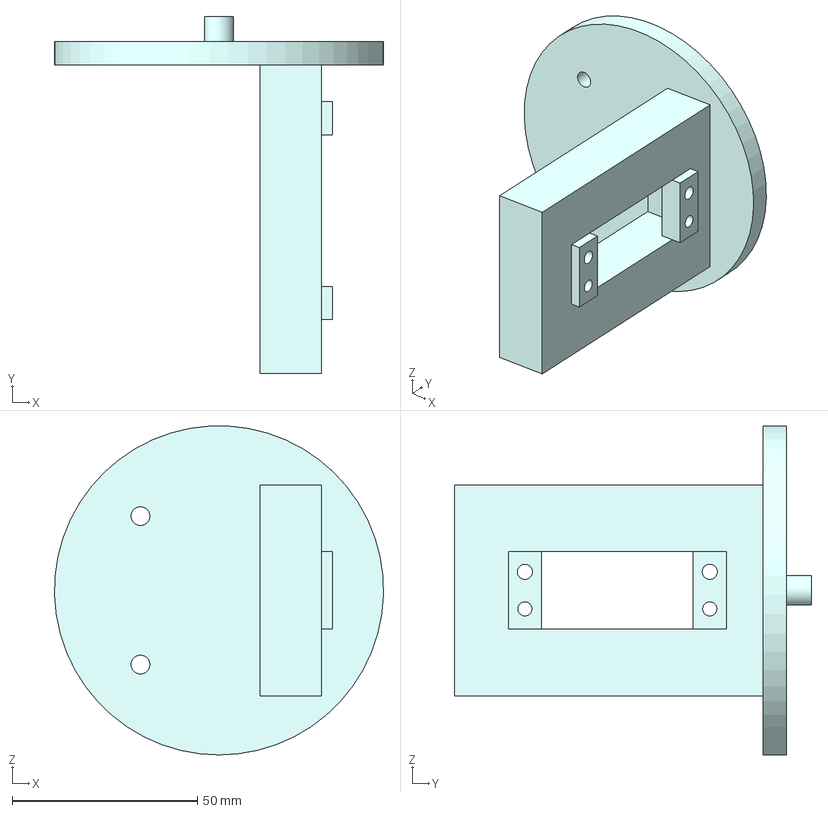
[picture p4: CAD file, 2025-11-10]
CAD/WRIST Part Studio - Wrist Servo Mount.step
88.9 x 96.5 x 88.8 mm

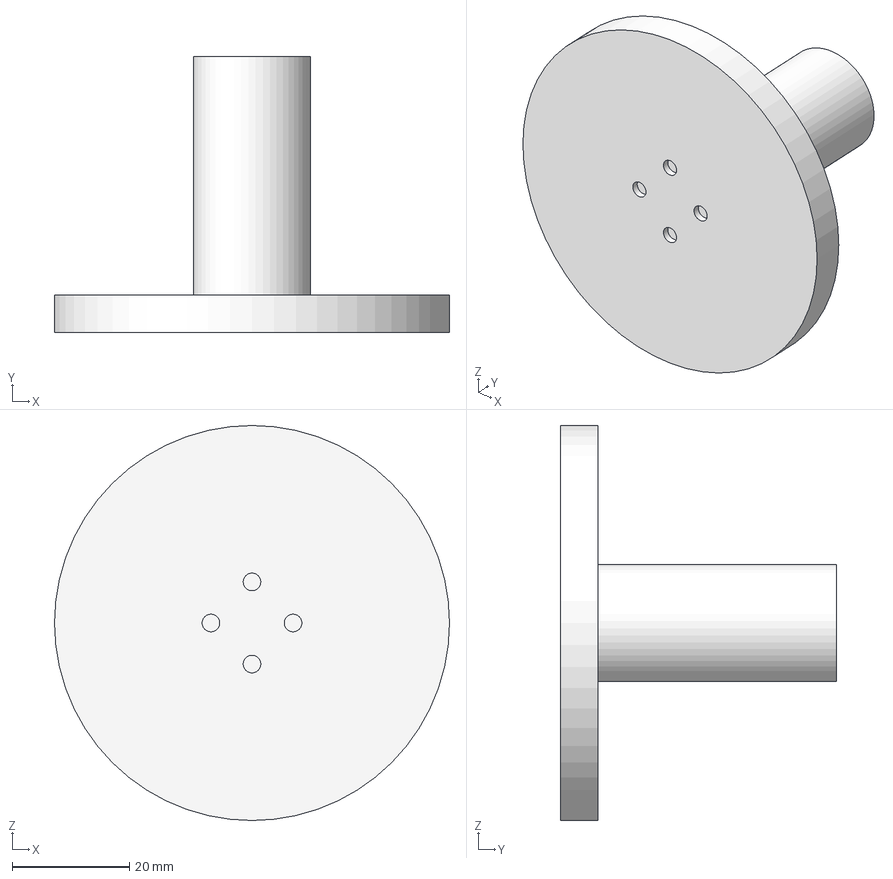
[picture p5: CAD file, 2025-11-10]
CAD/WRIST Part Studio - Wrist Servo Extension.step
67.3 x 47.0 x 67.3 mm

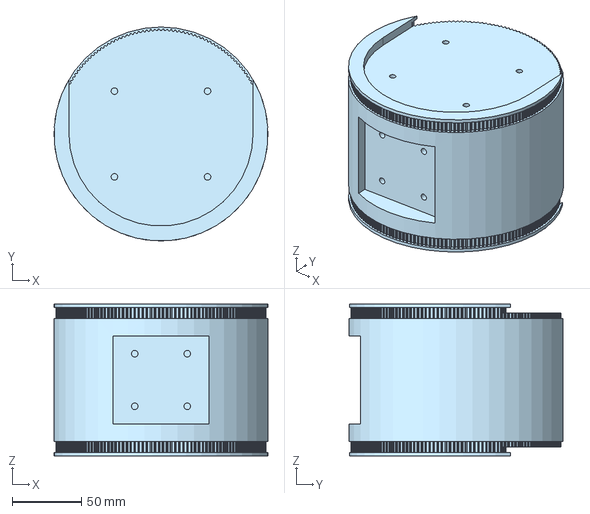
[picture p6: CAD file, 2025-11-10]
CAD/TILT Part Studio - PART D - Tilt Pulley (1).step
155.1 x 155.1 x 110.0 mm

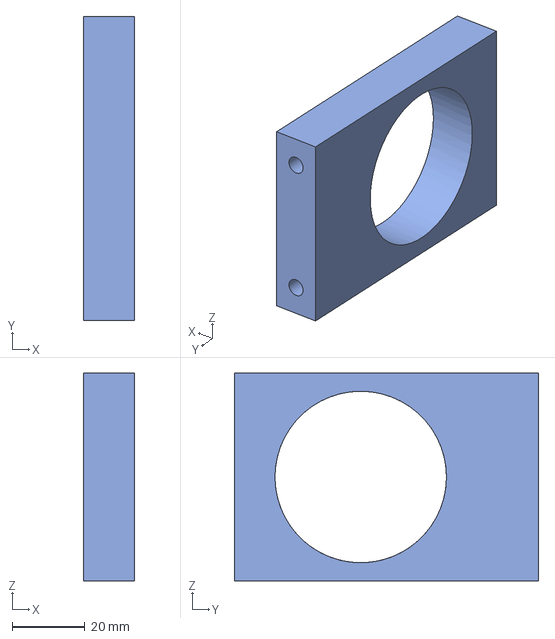
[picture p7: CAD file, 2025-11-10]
CAD/WRIST Part Studio - Wrist Servo Bearing Block.step
14.0 x 83.3 x 57.0 mm

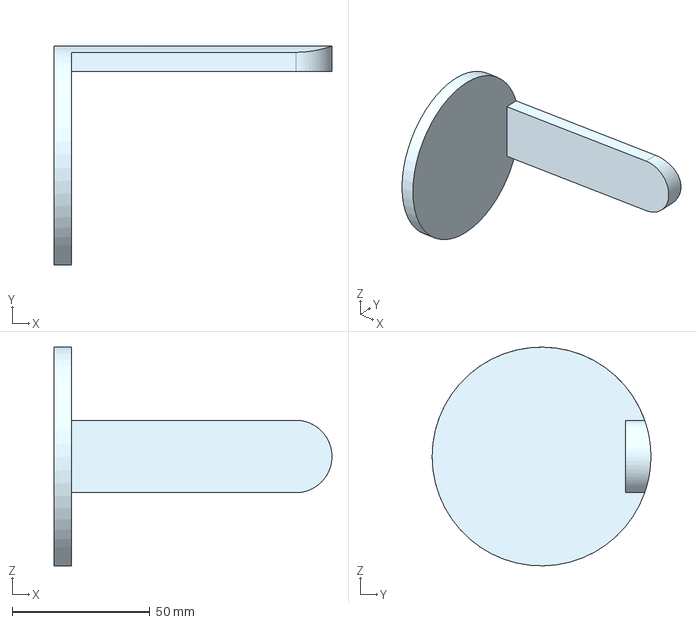
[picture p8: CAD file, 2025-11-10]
CAD/WRIST Part Studio - Grabber Mounting Plate.step
100.8 x 79.3 x 79.3 mm

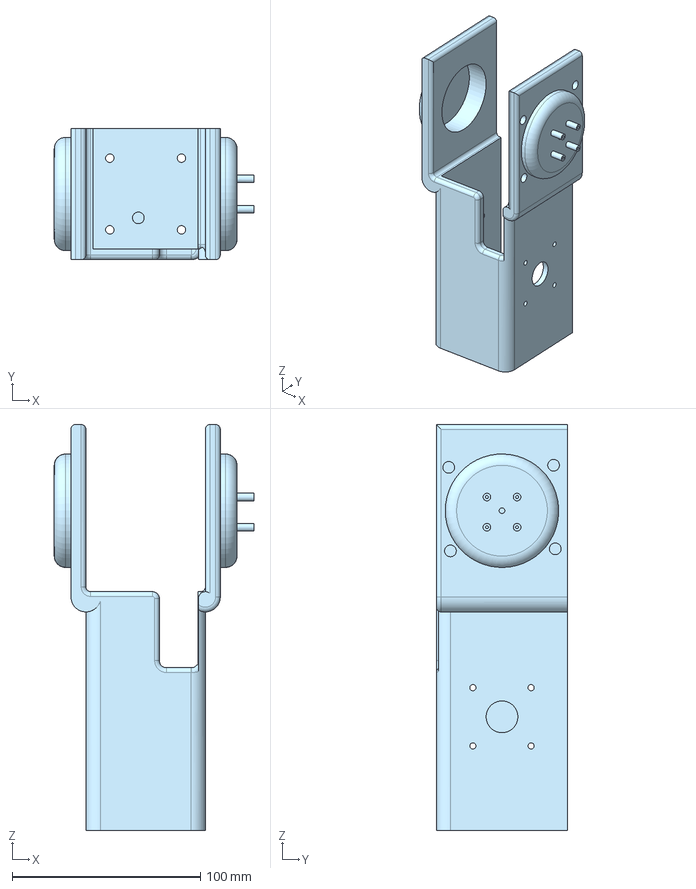
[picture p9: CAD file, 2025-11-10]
CAD/ARM Holder Part Studio.step
106.1 x 69.8 x 215.9 mm

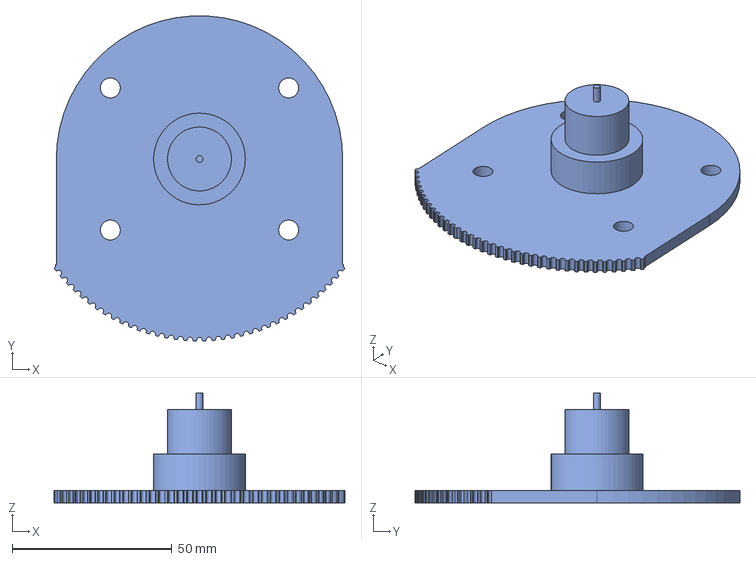
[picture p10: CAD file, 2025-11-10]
CAD/ARM Gear.step
90.8 x 101.6 x 34.3 mm

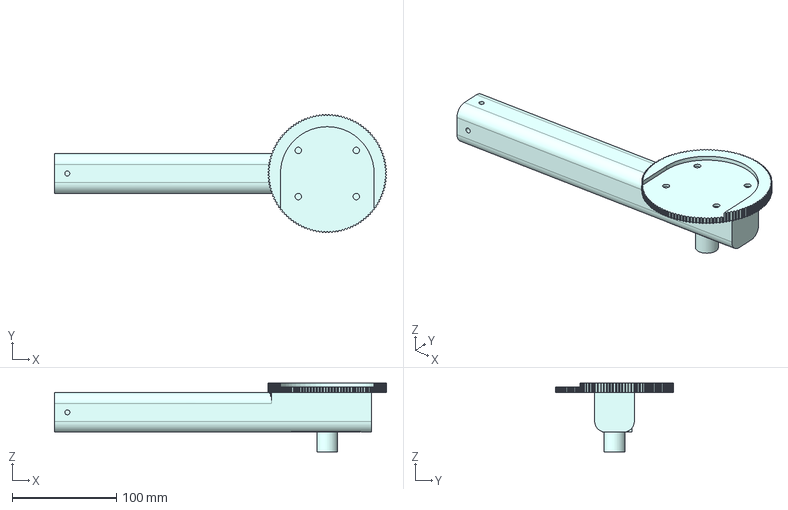
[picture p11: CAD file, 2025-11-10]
CAD/Arm.step
319.1 x 113.8 x 66.1 mm

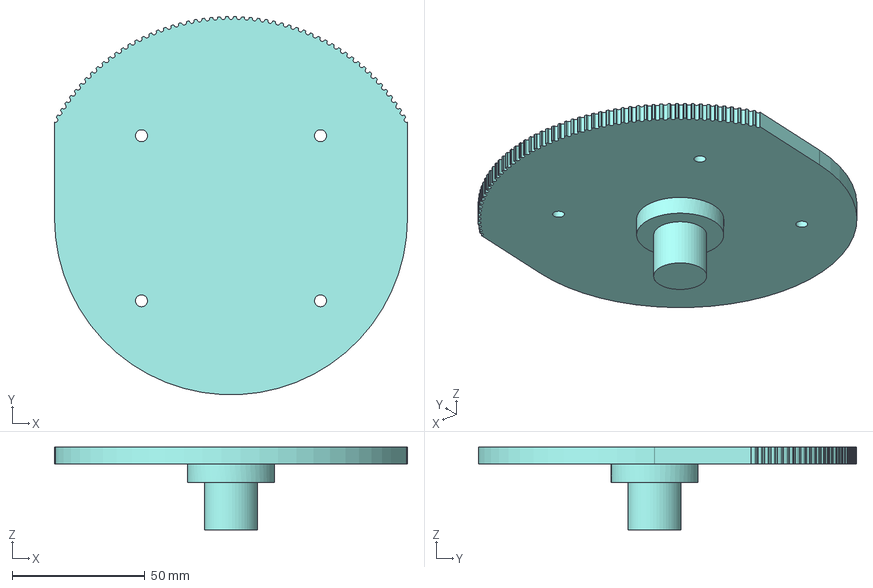
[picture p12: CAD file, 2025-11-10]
CAD/TILT Part Studio - PART C - Tilt Bearing Mount (1).step
133.0 x 142.4 x 31.1 mm

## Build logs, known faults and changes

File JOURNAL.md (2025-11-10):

<!--
  ===================    !!READ THIS NOTICE!!   ====================
  DO NOT edit this file manually. Your changes WILL BE OVERWRITTEN!
  This journal is auto generated and updated by Hack Club Blueprint.
  To edit this file, please edit your journal entries on Blueprint.
  ==================================================================
-->
**Total Time Spent: 50.5 Hours**

## 10/19/2025 - Researched current robot arm designs - 3.5 hours

**RESEARCH**

I researched a bunch of robot arm designs (10/18 and 10/19) that have already been made. I looked into what type of motors they use, which joints use what type of gearboxes, and what type of grabbers can be made.

Most of the arms were either made using a bunch of MG996R servos, but these arms were much smaller. The bigger arms were made using Nema 17 and Nema 23 stepper motors with planetary or cycloidal gearboxes attached. I want my design not to be too expensive to make, so I'm leaning towards using mainly Nema 17 motors and maybe 1 Nema 23 motor with either metal planetary gearboxes or printed plastic ones that I make myself. Most designs use ESP 32 since it is easier to connect to Wifi, which is what I am leaning towards as well.

The main costs for the project would be motors, gearboxes, motor drivers, the ESP32s, and the power supply, since I already have a 3d printer and filament. Most of the arm will be plastic except the motors and gearboxes. I haven't decided how many degrees of freedom it will have, as it will probably be dependent on what the total cost comes out to.



This is one of the arms I liked as it used mainly Nema 17's and isn't overcomplicated. The motors are connected to a small gear, which is connected to a larger gear using a belt. So it doesn't need complex gearboxes. The base uses one Nema 17 to turn the whole arm, but the part that tilts the arm uses two big Nema 23's both connected with a belt on either side. This seems a little excessive to me, so I would probably play around with what type of gearbox to use there instead and if it's possible, just to use one motor.

For the grabber, I want to start with just basic claws but I want it to have a easy mounting system so I can play around with pneumatics and a robot hand in the future.  

## 10/20/2025 4 PM - Created requirements, started design and CAD - 4 hours

After doing some more research and thinking, I decided:

**Goals:**

- Should be able to carry at least 0.5kg of weight.
- Should be able to have a reach of at least 15 inches.
- Parts should be < $150.

**Motor and Gearboxes:**

- The base will use one Nema 17 and a pulley system to rotate the robot arm
- The tilt function will use one Nema 17 motor with a pulley system and no gearbox for now. If it's needed later, I'll just 3d print a planetary gearbox.
- The 2 other joints will just use Nema 17 steppers and small pulley systems if needed.
- The grabber will use an MG996R Servo motor.
- If any joints need gearboxes, I can design planetary 3d printed gearboxes instead of buying metal ones to save on cost
- I will use a benchtop power supply to power it instead of buying a sepearte dedicated power supply.

I started making a CAD for the base rotation part and the tilt function in OnShape. I also started making a basic BOM of parts I might need.

This is the base of the robot arm where the electronics should fit. It has some holes on the side to mount onto a piece of plywood for added stability. The Nema 17 stepper motor mounts to the side without a gearbox. It will have a 20t pulley attatched to it with a GT2 timing belt that connects to the base of the robot onto a 280t pulley. The whole thing will rotate on tiny bearings on the edge of the base and then one bigger bearing in the middle.





That's how far I got during this CAD session. I still need to add the tiny bearings under the big pulley and finalize the distance between the centeres of the pully's to make sure there's a standard timing belt length I can by that's closed loop.  

## 10/20/2025 8 PM - Worked on CAD - 1.2 hours

I completed the base of the robot and added bearings, calculated the right distance between the motor pully and the big base pulley to make sure a 200mm belt will fit. I also added mounting brackets on the sides to mount onto a piece of plywood.



I also started working on the rotation assembly and the Nema 23 motor mounting.



This is how much time I spent on OnShape:



Next session, my goal is to finish the rotation part of it with all the motor mounts and pullys.

## 10/21/2025 12 AM - Continued CAD - 1 hour

I worked on the CAD for another hour. I figured out how to make the shaft longer on the stepper motor and how to fit all the bearings and pulleys. I also started working on the piece that will rotate the rest of the arm.





I worked for around an hour tonight.



## 10/21/2025 12 PM - Continued CAD - 1.2 hours 

Today I continued working on the CAD, and I finished most of the rotation part and created the mounting holes for the rest of the arm to mount onto the rotation part. I decided to use heat-sunk inserts for all the holes that need to be threaded.





## 10/21/2025 7 PM - Continued CAD - 3 hours

I worked on the arm part of it and calculated torque and pulley ratios based on the weight of the arm. The CAD is almost done, and after this, I'll start drawing out the wiring and designing a PCB as well as start some basic coding.





## 10/21/2025 10 PM - Finished CAD for now, researched PCB design - 1.8 hours

I finished the CAD for now. I'll come back to it later and edit the tiny things that need to be fixed. But it's done for the most part. I still need to make a grabber for the end of it as well. I'll edit the holes and clearances and wire openings once I have a BOM and an exact list of parts I want to get.



I started watching tutorials online on how to design PCB's since I have never done it before. My current plan is to have one big PCB that intakes power and has the stepper drivers and then a couple tiny PCB's for encoders and limit switches.



I spent basically 2 hours this session. My next steps are to start working on the electronics design and PCB and also think about and CAD a grabber design.  

## 10/22/2025 - Started PCB Schematics, Worked on BOM, Made a List of Parts - 4 hours

I did a bunch of research on how to design a PCB. I made a list of components I need and worked on the BOM. I also completed a lot of the schematics for the PCB. I decided on what drivers to use for each stepper as well as how it would be powered. Here's how far I got on the schmetatics for the PCB on EasyEDA.



## 10/23/2025 - Finished PCB Schematics, Worked on BOM - 4 hours

I finished the PCB schematics. It has three stepper motor drivers integrated for the three NEMA 17 Stepper Motors. The board I am using is an ESP32. I also have one bigger driver for the NEMA 23 stepper motor, which will be connected to the PCB with wires, not soldered on. I have three connectors for servos and six magnetic hall sensor connectors. I also have some LEDs that show when power is on, and when data is being transmitted. I also have a connection for an E-Stop button.



## 10/24/2025 - Worked on fixing PCB schematic issues - 0.8 hours

I had some issues with the footprints for the PCB schematic so I worked to fix those. I used a lot of user contributed footprints so that probably led to the issue. I just had to go in and replace a bunch of them.



## 10/25/2025 5 PM - Finished PCB Pretty Much - 3 hours  

I pretty much finished the PCB routing. I just need to do a GND copper fill later, which wasn't working correctly.







The price came out to $12 with shipping for five pcb's. My next steps are to finalize the CAD and make sure everything works, finish the BOM, and verify everything is good with the PCB and then I'll ship the project.

## 10/25/2025 6 PM - Worked on the BOM - 0.5 hours

I made my BOM spreadsheet and started adding parts to it, and also researched where to get parts. I looked into the types of Nema motors and how much torque they have, and the difference between sellers. I also looked into what type of hardware to use since I don't have any.



## 10/27/2025 - Worked on BOM and PCB - 3.5 hours 

A bunch of the footprints on the PCB ended up being wrong so I had to edit them. I also added most of the tiny electronics for the PCB onto the BOM. The total cost right now is $205 so I'll see if there's a way to bring that down. I retraced the PCB, replaced a couple of the connectors, and redid some of the wiring. The BOM is mostly done and the PCB should be done now. It took a while today because EasyEDA wouldn't let me update footprints without retracing the whole PCB and it also kept giving me errors. It also took a while finding each tiny component on AliExpress for the PCB that would fit the footprint.







## 10/28/2025 - Worked on Schematics - 3 hours

Apparently, all the driver footprints were wrong, so I had to redo that and all the tracing for that. I was using the wrong drivers so I replaced all of those with TMC2209's. I also worked on the BOM, and I'm almost done with that. My next steps are to make the arm look better and finalize all the details to make sure all the electronics that are on the BOM will work with the PCB. I also need to get the cost down as close to $200.



## 11/4/2025 3 PM - Finished Schematic, worked on PCB and BOM - 3 hours

I finished fixing and double-checking all the footprints on the schematic for the PCB. I also finished adding all the PCB parts to the BOM. I generated a PCB from the schematic and started the layout and tracing again. My next steps are to finish the BOM and PCB and make the CAD look better. I also need to make mounts for the magnet sensors in the CAD and tweak some things. I also need to make it look better overall, with filets, chamfers, etc. I had to get some of the electronics, like the little diodes and capacitors from DigiKey because I couldn't find the exact ones I wanted on Aliexpress with free shipping. I will move some of the other electronics to DigiKey before shipping this project because the electronics are a little cheaper on there and it doesn't force you to get 100 packs of everything. I also need to work on optimizing the BOM to bring the cost down since it's around $230 now and I still need to add filament once the CAD is finalized.



This is my current BOM: https://docs.google.com/spreadsheets/d/1jZwi7d67DiPdZLEvy5LfeC6HyOPPZ9pO3xaRMX1j6oo/edit?usp=sharing

This journal is from 11/3 just forgot to post it.  

## 11/4/2025 7 PM - Finished PCB - 2 hours

I finished the PCB and the BOM and started working on the CAD. This is a picture of the finished PCB. I made a copper fill for the GND on both the top and bottom layers and also added VIA's to connect them. I fixed the layout and made sure the capacitors are near the drivers to make sure they work properly, since that was one of the problems pointed out with my last design. I also changed a lot of the connectors to header pins to make it easier to solder and work with. I still need to add mounting holes on it to mount to a bracket later on. I previously had a XT60 connector soldered onto the PCB but I changed that to just a screw terminal which will connect onto a XT60 connector with wires. I thought this will be stronger than connecting the XT60 connector directly to the PCB every time. I added a banana-plug to XT60 adapter to the BOM since this is what will connect the bench power supply to the PCB. It will supply 24v.



I also worked on improving the CAD model to make it look better, and I worked on designing mounts for the magnet sensors.  

## 11/5/2025 - Worked on improving CAD - 1 hour

I chose to use M3 fasteners for everything and sourced the heat sink inserts and hardware. I started adding holes for those and I also started adding filets and more parts to the CAD to make it look better and more finished. My next steps are to finish adding all the remaining hardware (heated inserts, fastners, sensors) to the CAD and then finalizing how much filament I need so that I can add it to the BOM. Once that is done, I can create sample code and then ship the project.



## 11/8/2025 - Almost done with CAD and finished BOM - 4 hours

I finished adding all the fasteners to the CAD and I made sure all the hole sizes are right for the M3 screws and threaded inserts. I have a finalized design for the arm and I calculated how much filament I need to print it. I added that to the BOM. I also worked on a little cost optimization trying to find electronics on DigiKey for cheaper, since I'm already paying for shipping there. I added the AS5600 sensors into the CAD.

My next steps are:

- Double-check BOM accuracy
- Start making a basic code for the motors and controlling the arm using a custom UI
- Work on the GitHub repository - make the Readme and upload all the needed files.
- Finish cost optimization
- Maybe make a wiring diagram if needed for the GitHub?

Here's how the CAD looks right now:



Here's my updated BOM:

https://docs.google.com/spreadsheets/d/1jZwi7d67DiPdZLEvy5LfeC6HyOPPZ9pO3xaRMX1j6oo/edit?gid=0#gid=0

I also calculated how much filament I need roughly. These are the sliced parts.











So, roughly adding all of that, I got 1370g of filament. Rounding up to 1500g because I didn't include the smaller parts like the shaft and the parts for the end effector. I added filament to my BOM and changed the price so it only accounts for 1500g and I will pay the rest of the 500g myself since I would need to buy 2kg of filament.

(FYI: Made this journal over 3 different days.)  

## 11/9/2025 2 AM - Finished CAD and Worked on Github - 1.5 hours

Spent some more time today on the CAD, adding all the smaller details. I added the rest of the hardware to the CAD, mainly, and made sure the dimensioning for all the parts that were being mounted together was correct based on the hardware that I added to the BOM. I also started the GitHub page, and it should be finished tomorrow so that I can ship it.

I added another encoder to the bottom axle to get rotation values.







I added holes to make it easy to tighten the screws that will be in tight spots. I also added holes for heat-sunk inserts in the pictures above.



## 11/9/2025 6 PM - Finished Code, Finished GitHub, Shipped Project - 4.5 hours

Today I finally decided the CAD is finished. I have decided not to design an end-effector for now since I want to make a custom robot hand that will later attach to the end of this Robot Arm. I want to get the arm working with a fully custom UI before worrying about the end-effector.

This is the finished GitHub README:



I also wrote a basic code and uploaded it to GitHub and shipped my project.

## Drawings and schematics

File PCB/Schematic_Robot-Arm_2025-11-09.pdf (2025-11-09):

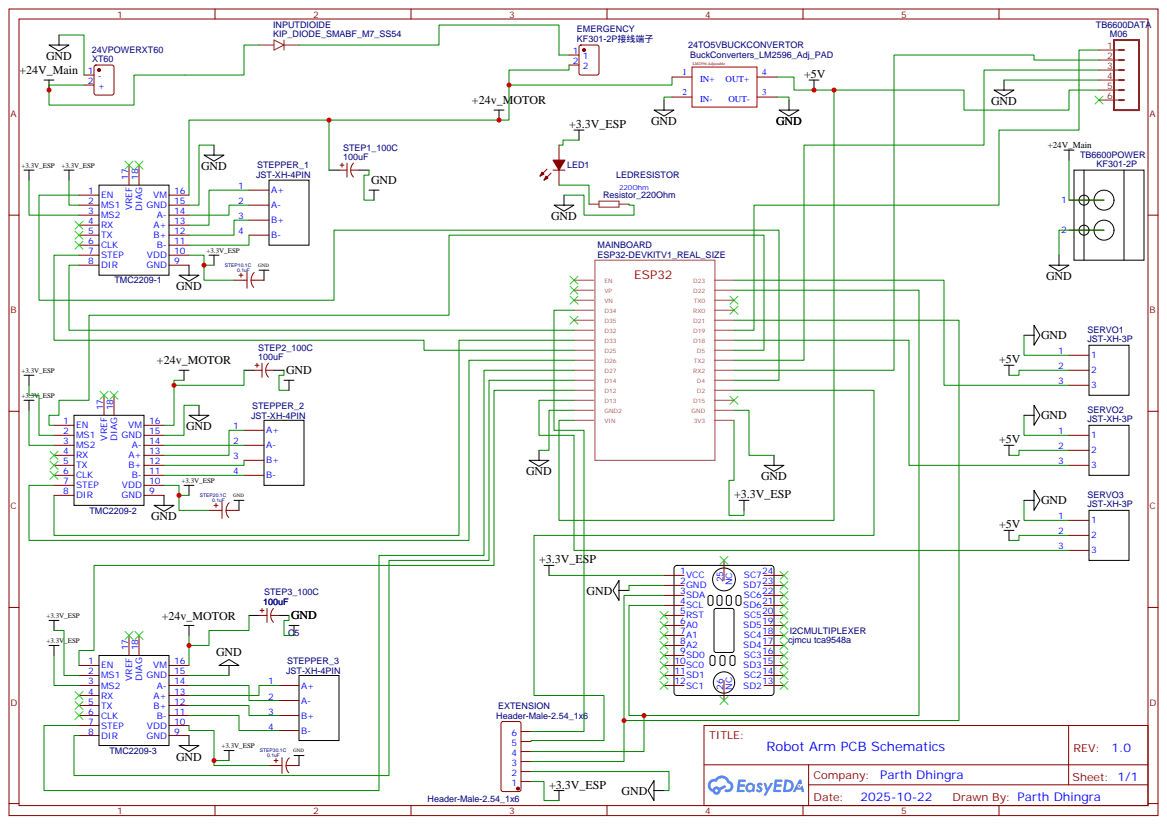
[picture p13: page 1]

Drawn By: Parth Dhingra

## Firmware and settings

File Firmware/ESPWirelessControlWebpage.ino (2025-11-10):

// === Robot Arm Web UI Control ===
// ESP32 Access Point + Web Server | Multi-stepper demo

#include <WiFi.h>
#include <WebServer.h>

#define EN_PIN 25
#define STEP1 26
#define DIR1 27
#define STEP2 14
#define DIR2 12
#define STEP3 18
#define DIR3 19

WebServer server(80);

void stepMotor(int stepPin, int dirPin, bool dir, int steps) {
  digitalWrite(dirPin, dir);
  for (int i = 0; i < steps; i++) {
    digitalWrite(stepPin, HIGH);
    delayMicroseconds(800);
    digitalWrite(stepPin, LOW);
    delayMicroseconds(800);
  }
}

void moveForward() {
  digitalWrite(EN_PIN, LOW);
  stepMotor(STEP1, DIR1, HIGH, 200);
  stepMotor(STEP2, DIR2, HIGH, 200);
  stepMotor(STEP3, DIR3, HIGH, 200);
}

void moveBackward() {
  digitalWrite(EN_PIN, LOW);
  stepMotor(STEP1, DIR1, LOW, 200);
  stepMotor(STEP2, DIR2, LOW, 200);
  stepMotor(STEP3, DIR3, LOW, 200);
}

void stopMotors() {
  digitalWrite(EN_PIN, HIGH);
}

String htmlPage = R"(
<!DOCTYPE html>
<html>
<head>
  <meta name='viewport' content='width=device-width, initial-scale=1.0'>
  <title>Robot Arm Control</title>
  <style>
    body {font-family: Arial; text-align:center; margin-top:40px; background:#111; color:white;}
    button {padding:15px 25px; margin:10px; font-size:18px; border:none; border-radius:8px; background:#008CBA; color:white;}
    button:hover {background:#005f7a;}
  </style>
</head>
<body>
  <h2>Robot Arm Web Control</h2>
  <button onclick="fetch('/forward')">Forward</button>
  <button onclick="fetch('/backward')">Backward</button>
  <button onclick="fetch('/stop')">Stop</button>
</body>
</html>
)";

void handleRoot() {
  server.send(200, "text/html", htmlPage);
}

void setup() {
  pinMode(EN_PIN, OUTPUT);
  pinMode(STEP1, OUTPUT); pinMode(DIR1, OUTPUT);
  pinMode(STEP2, OUTPUT); pinMode(DIR2, OUTPUT);
  pinMode(STEP3, OUTPUT); pinMode(DIR3, OUTPUT);
  digitalWrite(EN_PIN, HIGH); // disabled by default

  WiFi.softAP("RobotArm", "12345678");
  Serial.begin(115200);
  Serial.println("WiFi started! Connect to 'RobotArm' with password 12345678");
  Serial.println("Open http://192.168.4.1 in your browser.");

  server.on("/", handleRoot);
  server.on("/forward", [](){ moveForward(); server.send(200, "text/plain", "Forward"); });
  server.on("/backward", [](){ moveBackward(); server.send(200, "text/plain", "Backward"); });
  server.on("/stop", [](){ stopMotors(); server.send(200, "text/plain", "Stopped"); });

  server.begin();
}

void loop() {
  server.handleClient();
}

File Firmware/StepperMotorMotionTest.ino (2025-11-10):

// === Robot Arm Stepper Motor Test ===
// Parth Dhingra

#define EN_PIN   25
#define ESTOP_PIN 34

// Stepper 1
#define STEP1 26
#define DIR1  27

// Stepper 2
#define STEP2 14
#define DIR2  12

// Stepper 3
#define STEP3 18
#define DIR3  19

int stepDelay = 800; // microseconds (speed control)

void stepMotor(int stepPin, int dirPin, bool dir, int steps) {
  digitalWrite(dirPin, dir);
  for (int i = 0; i < steps; i++) {
    digitalWrite(stepPin, HIGH);
    delayMicroseconds(stepDelay);
    digitalWrite(stepPin, LOW);
    delayMicroseconds(stepDelay);
  }
}

void setup() {
  Serial.begin(115200);
  pinMode(EN_PIN, OUTPUT);
  pinMode(ESTOP_PIN, INPUT_PULLUP);
  pinMode(STEP1, OUTPUT);
  pinMode(DIR1, OUTPUT);
  pinMode(STEP2, OUTPUT);
  pinMode(DIR2, OUTPUT);
  pinMode(STEP3, OUTPUT);
  pinMode(DIR3, OUTPUT);
  digitalWrite(EN_PIN, LOW); // enable all
  Serial.println("Stepper test started.");
}

void loop() {
  if (digitalRead(ESTOP_PIN) == LOW) {
    Serial.println("E-STOP pressed! Disabling motors.");
    digitalWrite(EN_PIN, HIGH);
    delay(500);
    return;
  }

  // Forward direction
  Serial.println("Moving forward...");
  stepMotor(STEP1, DIR1, HIGH, 200);
  stepMotor(STEP2, DIR2, HIGH, 200);
  stepMotor(STEP3, DIR3, HIGH, 200);
  delay(500);

  // Backward direction
  Serial.println("Moving backward...");
  stepMotor(STEP1, DIR1, LOW, 200);
  stepMotor(STEP2, DIR2, LOW, 200);
  stepMotor(STEP3, DIR3, LOW, 200);
  delay(500);
}

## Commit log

2025-11-10 Update and rename Robot Arm BOM - BOM (1).csv to bom.csv
    [bom.csv]
2025-11-13 Update and rename Robot Arm BOM - BOM (2).csv to bom.csv
    [bom.csv]
2025-11-26 Update and rename Robot Hand BOM - Sheet1.csv to bom.csv
    [bom.csv]
2025-11-26 Update and rename Robot Arm BOM - BOM (3).csv to bom.csv
    [bom.csv]
